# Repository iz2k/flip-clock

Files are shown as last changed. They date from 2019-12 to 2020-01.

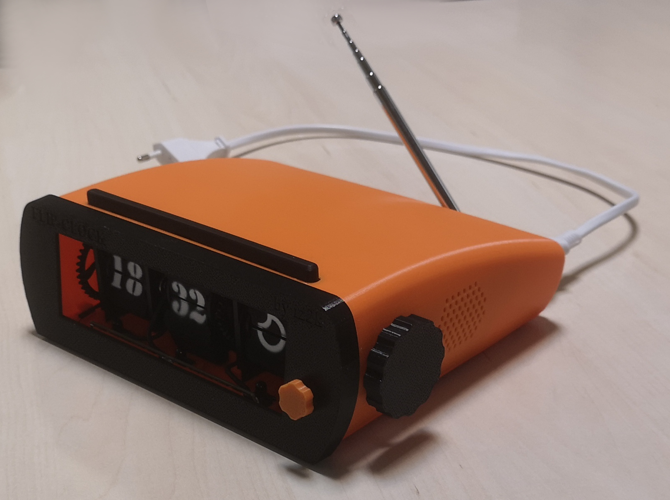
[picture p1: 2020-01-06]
imgs/right.jpg

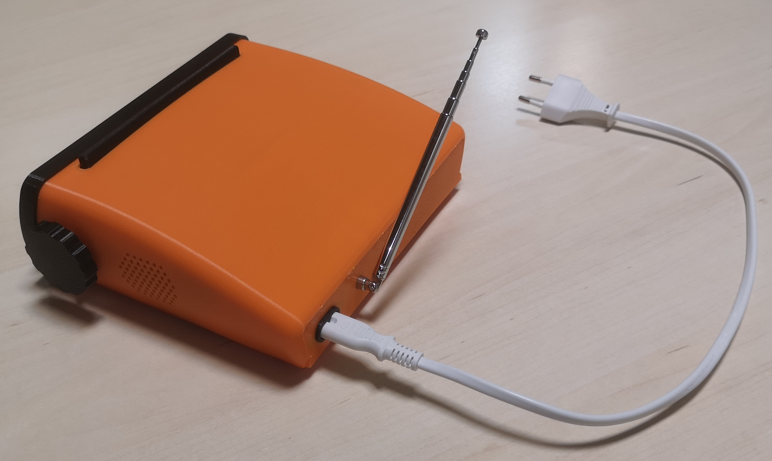
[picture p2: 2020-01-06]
imgs/back.jpg

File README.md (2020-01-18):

# Flip-Clock

The Flip-Clock is an old stylish, classic alarm clock with up to date features, such as automatic time adjustment, weather forecast, FM radio or Spotify playback. The device consists of three 3D printed flip digits, a  PCB with integrated drivers for the digit controlling stepper motors and a Raspberry Pi 3 A+ with 3W speakers to run the main code.

All the mechanics and electronics are mounted within an 3D printed elegant cover. Additionally, a snoozer bar, two rotary encoders and a RGBW LED strip are included for the user interface.

| front | right |
| - | - |
| left | back |

Find additional info about each design in:
* <a href="https://github.com/iz2k/flip-clock/tree/master/3d">3D parts</a>
* <a href="https://github.com/iz2k/flip-clock/tree/master/pcb_hw">PCB hardware</a>
* <a href="https://github.com/iz2k/flip-clock/tree/master/pcb_fw">PCB firmware</a>
* <a href="https://github.com/iz2k/flip-clock/tree/master/rpi_sw">RPi3 software</a>

Flip-Clock in action (https://youtu.be/fy7IPMUoMU4 "Flip-Clock in action")

# Parts

## 3D printed flip digits

Each flip digit consists of a support structure with two bearings. The axle is placed inside the bearings holding two flap holders. All the flaps are mounted within those holders. The movement of the digit is achieved with a stepper motor and two gears. An IR transmitter and an IR receiver are palced on the top and on the bottom of the flaps to detect transitions. Additionally, a limit switch is placed close to the gears to synchronize with it each turn.

### Subparts

1. Support structure
2. Bearings (<a href="https://www.amazon.es/gp/product/B07CWLGNJ5/ref=ppx_yo_dt_b_asin_title_o07_s01?ie=UTF8&psc=1">623-2RS</a>)
3. Axle
4. Flap holders
5. Flaps
6. Gears
7. Stepper motor (<a href="https://www.amazon.es/gp/product/B07LCFKJB8/ref=ppx_yo_dt_b_asin_title_o01_s00?ie=UTF8&psc=1">28BYJ-48</a>)
8. IR transmitter (<a href="https://www.amazon.es/gp/product/B07F3W2SP4/ref=ppx_yo_dt_b_asin_title_o07_s00?ie=UTF8&psc=1">IR diode</a>)
9. IR receiver (<a href="https://www.amazon.es/gp/product/B07F3W2SP4/ref=ppx_yo_dt_b_asin_title_o07_s00?ie=UTF8&psc=1">IR photodiode</a>)
10. Limit switch (<a href="https://www.amazon.es/gp/product/B07GKS9XC7/ref=ppx_yo_dt_b_asin_title_o05_s00?ie=UTF8&psc=1">CLW1093</a>)



## FlipDigitController PCB
The FlipDigitController PCB includes a microcontroller and drivers to control the stepper motors. Additionally, the PCB also handles the IR transmitter and receiver to detect flap transitions and the limit switch for automatic synchronization of the axle. The PCB has an UART interface for the abstraction layer protocol.

The current version of the PCB can handle up to two flip digits at the same time. For the FlipClock device two units of the PCB have been used: one to control hours and minutes flaps, and another one to control weather flaps.

| Block diagram | Layout |
|---|---|
| | |

### Subparts
1. <a href="http://www.ti.com/product/MSP430FR2433">MSP430FR2433 MCU</a>
2. <a href="http://www.ti.com/product/INA333?keyMatch=INA333&tisearch=Search-EN-everything&usecase=part-number">INA333 comparators</a>
3. <a href="https://www.ti.com/product/ULN2003A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">ULN2003A drivers</a>

## 3D printed cover


### Subparts
1. 3D printed top cover
2. 3D printed bottom cover
3. 3D printed front cover
4. 3D printed back cover

## Rotary encoders
For the user interface two rotary encoders have been used. The used encoders can detect steps in both directions, and include a built-in switch. One of the encoders is used to control the volume (up/down/mute), whereas the other encoder controls the audio device (FM Radio/Spotify/OFF)

| Wheels | Encoders |
| --- | --- |
|| |

### Subparts
1. 3D printed volume wheel
2. 3D printed control wheel
3. <a href="https://www.mouser.es/ProductDetail/BI-Technologies-TT-Electronics/EN11-HSM1AF15?qs=u1MaZ2%2F4xgsleMatSs8Sqg==">TT EN11-HSM1AF15</a> Rotary Encoders

## Snooze bar
A snooze bar is included on top of the FlipClock device. This bar can be used to trigger the nightlight by default, or to stop/snooze the alarm when it has been triggered. Tactile switches are placed under the bar to detect when it is pressed.

| Bar | Switch |
| --- | --- |
|bar | switch

### Subparts
1. 3D printed snooze bar
2. <a hlink="https://octopart.com/evq-q2s03w-panasonic-1199659">EVQ-Q2S03W</a> tactile switches

## NeoPixel RGBW Stick
Two NeoPixel RGBW LED sticks have been included in the front of the FlipClock in order to provide nightlight and light-sign functions to the device.

neopixel

### Subparts
1. <a href="https://www.adafruit.com/product/2868">NeoPixel RGBW Stick</a>

## 3W Speakers


### Subparts
1. <a href="https://www.adafruit.com/product/1669">Stereo Enclosed Speaker Set - 3W 4 Ohm</a>

## FM radio tunner (RTL-SDR)

| RTL-SDR dongle | FM antenna |
| --- | --- |
|||

### Subparts
1. <a href="https://www.amazon.es/gp/product/B013Q94CT6/ref=ppx_yo_dt_b_asin_title_o06_s00?ie=UTF8&psc=1">RTL-SDR dongle</a>
2. <a href="https://www.amazon.es/gp/product/B07CJYRWXQ/ref=ppx_yo_dt_b_asin_title_o01_s00?ie=UTF8&psc=1">FM antenna</a>

## Raspberry Pi 3 A+
|Raspberry Pi 3 Model A+|Adafruit I2S 3W Stereo Speaker Bonnet|
|--|--|
|||

### Subparts
1. <a href="https://www.raspberrypi.org/products/raspberry-pi-3-model-a-plus/">RPI3 A+</a>
2. <a href="https://www.adafruit.com/product/3346">Adafruit I2S 3W Stereo Speaker Bonnet</a>

## Power Supply
|Power Supply Module| PSM Housing|
|--|--|
|||

### Subparts
1. <a href="https://www.digikey.com/product-detail/en/mean-well-usa-inc/PS-05-5/1866-5411-ND/7705819">PS-05-5</a> power supply module
2. 3D printed housing

# Wiring

The correct wiring to connect the different electronics is as follows:

PSM connection:

| Subpart | PIN | PIN | Subpart |
| -- | -- | -- | --|
| RPI3 | 5V | 5V | PSM |
| RPI3 | GND | GND | PSM |

NeoPixel connection:

| Subpart | PIN | PIN | Subpart |
| -- | -- | -- | --|
| NeoPixel | DIN | MOSI | RPI3 |
| NeoPixel | 5VDC | 5V | RPI3 |
| NeoPixel | GND | GND | RPI3 |

Snooze Bar connection:

| Subpart | PIN | PIN | Subpart |
| -- | -- | -- | --|
| Snooze Bar | SW0 | GPIO 4 | RPI3 |
| Snooze Bar | SW1 | GPIO 17 | RPI3 |

Volume Encoder<sup>1</sup> connection:

| Subpart | PIN | PIN | Subpart |
| -- | -- | -- | --|
| Volume Encoder | SW0 | GPIO 24 | RPI3 |
| Volume Encoder | SW1 | GPIO 25 | RPI3 |
| Volume Encoder | ROT0 | GPIO 27 | RPI3 |
| Volume Encoder | ROT1 | GPIO 23 | RPI3 |
| Volume Encoder | GND | GPIO 22 | RPI3 |

Control Encoder<sup>1</sup> connection:

| Subpart | PIN | PIN | Subpart |
| -- | -- | -- | --|
| Control Encoder | SW0 | GPIO 5 | RPI3 |
| Control Encoder | SW1 | GPIO 6 | RPI3 |
| Control Encoder | ROT0 | GPIO 12 | RPI3 |
| Control Encoder | ROT1 | GPIO 16 | RPI3 |
| Control Encoder | GND | GPIO 13 | RPI3 |

Flip-Clock-Controller PCB:

|Subpart | PIN | PIN | Subpart |
|--|--|--|--|
|RPI3 | 3.3V | 3.3V | Flip-Clock-Controller PCB 1 (HHMM)|
|RPI3 | 3.3V | 3.3V | Flip-Clock-Controller PCB 2 (WW)|
|RPI3 | TX | RX | Flip-Clock-Controller PCB 1 (HHMM)|
|Flip-Clock-Controller PCB 1 (HHMM) | TX | RX | Flip-Clock-Controller PCB 2 (WW)|
|Flip-Clock-Controller PCB 2 (WW) | TX | RX | RPI3|

1: For ease of connectivity, all pins of rotary encoders are routed to GPIOs. These GPIOs will be configured as required with pull resistors or fixed voltages via software.

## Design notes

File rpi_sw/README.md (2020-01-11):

# Flip-Clock RPI3 A+: software design

The software in the Raspberry Pi 3 Model A+ is in charge of controlling the global funtionality of the device. It connects to the internet to get the current time, weather forecast and audio streams. All of it is performed according to the user interaction with the rotatory wheels, snooze bar and configuration files.

The software is written in Python 3 and makes use of several python libraries and external CLI applications.

## RPI3 setup

In order to run the Flip-Clock software on the Raspberry Pi 3 Model A+, the device has to be set up correctly. The software has been developed and tested on the `Raspbian Buster Lite (2019-09-26)` OS (without desktop). In any case, it should be possible to run it on other versions of Raspian.

### WPA supplicant

The first parameter to set up is the WiFi connectivity. The Model A+ does not have an ethernet connector, so the connectivity to internet is provded by WiFi. The easiest way to get the wifi connection working, is to use the WPA supplicant. As explained in <a href="https://howchoo.com/g/ndy1zte2yjn/how-to-set-up-wifi-on-your-raspberry-pi-without-ethernet">this</a> post, you need to include a file called `wpa_supplicant.conf` in the `/etc/wpa_supplicant/` folder.

This can also be achieved connecting the SD card with Raspian to your Windows/MacOS computer and copying the `wpa_supplicant.conf` file into the FAT32 `/boot` partition. Raspian will copy the file to the correct location in the next boot of the pi.

The content of the file has to be as follows:

````
ctrl_interface=DIR=/var/run/wpa_supplicant GROUP=netdev
update_config=1
country=ES

network={
	ssid="My SSID"
	psk="My Password"
	key_mgmt=WPA-PSK
}
````

You can add multiple networks if you want the device to connect to the internet in different locations.

### I2S audio (PWM)

In order to make the sound work with the Adafruit I2S 3W Stereo Speaker Bonnet, you can use the <a href="https://github.com/adafruit/Raspberry-Pi-Installer-Scripts">script on their github</a>. If you do not want to deep in in the details, just run the following curl script:

If you do not have curl already installed on your system, just do it:

````
sudo apt-get update
sudo apt-get install curl
````

And then execute the script:

````
curl -sS https://raw.githubusercontent.com/adafruit/Raspberry-Pi-Installer-Scripts/master/i2samp.sh | bash
````

### UART

The UART is required to communicate with the Flip-Clock-Contorller PCB. As by default in Raspian the UART is assigned to the console, you will need to disable the console and enable the software UART `/dev/ttyS0`.

This can be easily achieved using the `raspi-config` tool. Go to the `Interfacing Options` section, and then to `Serial`.

### SPI

In order to control the NeoPixel stick, we will use the <a href="https://github.com/jgarff/rpi_ws281x">rpi_ws281x</a> python library. This library supports controlling the stick using PCM, PWM or SPI. Given that we are using PCM for audio and PWM for PiGPIO (see in dependencies), we will use the SPI for the NeoPixel stick.

Many distributions have a maximum SPI transfer of 4096 bytes. This can be changed in /boot/cmdline.txt by appending

````
spidev.bufsiz=32768
````

On the RPi 3 you have to change the GPU core frequency to 250 MHz, otherwise the SPI clock has the wrong frequency. Do this by adding the following line to /boot/config.txt and reboot.

````
core_freq=250
````

SPI requires you to be in the gpio group if you wish to control your LEDs without root.

## Dependencies

Once the hardware of the Raspberry Pi has been correctly set-up, the dependencies of the project have to be installed.

### Python 3

Given that the Flip-Clock software is written in python, you will need the correct interpreter. Install python 3 as follows:

````
sudo apt-get install python3
````

Additionally, you will need to install several dependencies referenced in the project using `pip3`:

````
sudo pip3 install time
sudo pip3 install os
sudo pip3 install datetime
sudo pip3 install rpi_ws281x
sudo pip3 install pigpio
sudo pip3 install queue
sudo pip3 install wave
sudo pip3 install alsaaudio
sudo pip3 install subprocess
sudo pip3 install shlex
sudo pip3 install darksky
sudo pip3 install lxml 
sudo pip3 install subprocess
sudo pip3 install shlex
sudo pip3 install flask
sudo pip3 install threading
sudo pip3 install wtforms 
sudo pip3 install decimal
````

I may be missing some module. In case you get an error of some module missing, just install it using `pip3`.

### PiGPIO (PWM)

<a href="http://abyz.me.uk/rpi/pigpio/index.html">PiGPIO</a> is a library for the Raspberry Pi which allows control of the General Purpose Input Outputs (GPIO). This library has been selected as it provides a fast response time, which is required for the rotary encoders.

Install the PiGPIO deamon as follows:

````
sudo apt-get update
sudo apt-get install pigpio python-pigpio python3-pigpio
````

In order to make the pigpio deamon run on startup you can either enable it via systemctl, or add a root crontab job. 

As explained in <a href="https://www.raspberrypi.org/forums/viewtopic.php?t=103752#p717150">this</a> post, use

````
sudo crontab -e
````

to edit the root crontab and add the following line to the end. Then ctrl-o return ctrl-x to exit.

````
@reboot              /usr/bin/pigpiod -t 0
````

Note that it is necessary to use the `-t 0` argument in order to launch the `pigpio` deamon in `PWM` mode instead of the default `PCM` mode. Failing to do so will break the audio that is already using the PCM hardware.

### mplayer

In order to play audio files, or in this case to play the audio returned by google translate for TTS purposes, install `mplayer`:

````
sudo apt-get install mplayer
````

### SoftFM

In order to synthonize FM radio using the RTL-SDR stick, we will use an improved version of `rtl_fm` called `softfm`. It gets better results with poor quality radio signals. We will have to build the binary for the RPI3 ourselves, but it is quite straightforward.

#### Install RTL-SDR

First install the RTL-SDR library in order to have the required header files.

````
sudo apt-get install rtl-sdr
````

You can check if the RTL-SDR usb dongle is recognized as follows:

````
rtl_test
````

Yous should see something similar to this:

````
Found 1 device(s):
  0:  Generic, RTL2832U, SN: 77771111153705700
````

#### Build SoftFM

As explained in the <a href="https://github.com/jorisvr/SoftFM">SoftFM github repository</a>, to install SoftFM, download and unpack the source code and go to the top level directory. 

First make sure you have the build tools installed:

````
sudo apt-get install libusb-1.0-0-dev
sudo apt-get install build-essential
````

Then do like this:

````
mkdir build
cd build
cmake ..

make
````

You can test if the generated binary works fine:

````
./softfm -f <radio-frequency-in-Hz>
````

### Tizonia
<a href="http://tizonia.org/">Tizonia</a> is a cloud music player from the Linux terminal. It supports some of the major cloud music services: Spotify, Google Play Music, SoundCloud, YouTube, Plex and Chromecast. We will use this CLI player to add playback support from Spotify. It should be straightforward to extend playback support for the other supported audio streaming platforms, but this has not been implemented for now, as I am currently a Spotify user.

Install Tizonia as follows:

````
curl -kL https://github.com/tizonia/tizonia-openmax-il/raw/master/tools/install.sh | bash
````

### Raspotify (optional)

Even if Tizonia is great and allows us to stream music from spotify from code, it will not show our Flip-Clock as a Spotify device in our network. If you want to use the Flip-Clock as a smart speaker that shows as a spotify device and can be controlled by your smartphone, just install Raspotify. This is optinal, as the rest of the software does not depend on raspotify to function.

To install raspotify, follow the instructions on the <a href="https://github.com/dtcooper/raspotify">Raspotify github repository</a>:

````
curl -sL https://dtcooper.github.io/raspotify/install.sh | sh
````

## Flip-Clock software

In order to run the Flip-Clock software, just copy all the files to the desired location. I used `/usr/share/flip-clock`. for ease of use, make the main file executable:

````
chmod +x flip-clock.py
````

You can also add a symbolic link to `/usr/bin` in order to make it visible to $PATH.

````
ln -s /usr/share/flip-clock/flip-clock /usr/bin/flip-clock
````

To run the software, just execute it:

````
./flip-clock
````

### Autostart (systemd unit file)

In order to make the Flip-Clock software run automatically on every boot, you can create a systemd unit file. I have included a reference unit file in the `autostart` folder.

Copy the flip-clock.service file to `/etc/systemd/system/` folder:

````
sudo cp  flip-clock.service /etc/systemd/system/ flip-clock.service
````

The reference unit file redirects the output to syslog using the method explained <a href="https://stackoverflow.com/questions/37585758/how-to-redirect-output-of-systemd-service-to-a-file">here</a>. In order to configure syslog to handle the incoming stream, copy the `flip-clock.conf` configuration file to `/etc/rsyslog.d/`

````
sudo cp flip-clock.conf /etc/rsyslog.d/
````

Now make the log file writable by syslog:

````
chown root:adm /var/log/flip-clock.log
````

Restart rsyslog:

````
sudo systemctl restart rsyslog
````

Now the stdout/stderr of flip-clock will still be available through journalctl (`sudo journalctl -u flip-clock`) but they will also be available in `/var/log/flip-clock.log`.

Reload the systemctl daemon to read the new unit file.

````
sudo systemctl daemon-reload
````

Enable the flip-clock service to run on startup:

````
sudo systemctl enable flip-clock.service
````

Run the flip-clock service without rebooting:

````
sudo systemctl start flip-clock.service
````

### Code structure

The code structure is as follows:

````
flip-clock
 >> /config/
    >> Configuration XML files.
 >> /frontend/
    >> Flask web frontend files.
 >> /lib/
    >> Project specific library files.
 >> /sounds/ 
    >> PCM format sound files.
 >> flip-clock.py
    >> Main program.
````

#### Main program

The main program generates instances of the library classes to control the different peripherals, and keeps track of the main program flow with the user interaction. The callbacks of the rotary encoders and switches as well as the frontend event queue are read in this script to obtain the desired functionality.

#### Libraries

For each peripheral a project specific library has been created.

##### Clock

The clock library gets the current time from the system, the weather forecast form the DarkSky API and handles the UART communication towards the FlipClockPCB accordingly.

##### Audio

The audio library controls the audio of the device through alsamixer. It controls the volume and allows playing simple PCM files and converting text to audio using google translate as TTS.

##### LED

The LED library controls the Neopixel sticks to generate light signaling as requested by the main program.

##### IO

The IO library handles the rotary encoders and switches.

##### Spotify

The Spotify library handles the spotify playback through Tizonia.

##### Radio

The Radio library handles the radio synthonization through SoftFM.

##### Alarm

The Alarm library handles the alarm settings to trigger the corresponding events when the time comes.

#### Front-end (flask)

The flask based web front-end allows the user to configure the clock, radio stations, spotify playlists and alarm configurations via a web browser accesible through: `http://hostname:5000`

#### Configuration files

The configuration files store the configuration of the different services.

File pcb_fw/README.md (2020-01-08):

# Flip-Clock-Controller PCB: firmware design

The firmware of the Flip-Clock-Controller PCB has been designed using Code Composer Studio. The device is controled via standard UART communication at 115200 bauds. Here are the supported commands. The commands are decoded after receiving a return character.

| Command | Description |
|--|--|
| i | Shows current situation of HH and MM digits |
| hXX | Move HH digit to poxition XX (where XX are two decimal digits) |
| mXX | Move MM digit to poxition XX (where XX are two decimal digits) |
| sh | Sync HH digit. Keeps on moving flaps until the limit switch finds the synchronization position. |
| sm | Sync MM digit. Keeps on moving flaps until the limit switch finds the synchronization position. |
| chXX | Calibrate HH value in synchronization position to XX (where XX are two decimal digits)|
| cmXX | Calibrate MM value in synchronization position to XX (where XX are two decimal digits)|

In order to add the weather forecast digit, a second Flip-Clock-Controller PCB has been used. For control simplicity, and given that the PCB echoes the received UART characters, the UART of the two PCBs have been connected in daisy-chain.

|Subpart | PIN | PIN | Subpart |
|--|--|--|--|
|RPI3 | TX | RX | Flip-Clock-Controller PCB 1 (HHMM)|
|Flip-Clock-Controller PCB 1 (HHMM) | TX | RX | Flip-Clock-Controller PCB 2 (WW)|
|Flip-Clock-Controller PCB 2 (WW) | TX | RX | RPI3|

For the second PCB, a modified version of the firmware has been used, where the following commands are included:

| Command | Description |
|--|--|
| y | Shows current situation of WW digit |
| wXX | Move WW digit to poxition XX (where XX are two decimal digits) |
| sw | Sync WW digit. Keeps on moving flaps until the limit switch finds the synchronization position. |
| cwXX | Calibrate WW value in synchronization position to XX (where XX are two decimal digits)|

## Flashing the MSP430

I have used a <a href="http://www.ti.com/tool/MSP-FET">MSP-FET</a> device as I already own one. If you do not have one, a basic <a href="http://www.ti.com/tool/MSP-EXP430FR2433?keyMatch=MSP430FR2433%20LAUNCHPAD&tisearch=Search-EN-everything">launchpad</a> can be used to program an external device. Finally, it is also possible to flash the device via the UART BSL using <a href="http://www.ti.com/tool/UNIFLASH?keyMatch=UNIFLASH&tisearch=Search-EN-everything&usecase=part-number">Uniflash</a> software.

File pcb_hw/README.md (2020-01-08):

# Flip-Clock-Controller PCB: hardware design

The Flip-Clock-Controller PCB has been designed using Circuit Maker. Unluckily, there is now way to export the design to standard design formats out of their cloud. Thus, only the fabrication outputs and the documentation is included.

The Flip-Clock-Contorller PCB features a low power MSP430FR2433 microcontroller to handle the control of the flap digits. For each digit a stepper motor driver is included. The PCB also includes the analog front-end to handle the IR transmitter and receiver so that each time a flap falls down the MCU can detect it. Additionally, a limit switch is included so that every time the gear return to the initial position the MCU can detect the position and synchronize continuously to avoid number offset due to missed flap transitions (that rarely happen). The control interface of the PCB is 3.3V UART.

Even if a integrated 5V to 3.3V DCDC is included in the design, I finally decided to bypass it and use the 3.3V provided by the Raspberry Pi 3. The rest of the components are easy to solder manually with a soldering air gun.



## Schematics



## Layout



## 3D



## Fabrication outputs

The following fabrication outputs are included:
* Gerber files
* NC Drill files
* Bill Of Materials

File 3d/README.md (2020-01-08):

# Flip-Clock 3D design

The design of the 3D printed parts has been done using Fusion 360. The document flip-clock.f3d contains the complete design, including the external electronic components.

For the internal parts of the Flip Digits, ABS filament has been used for enhanced mechanical robustness. Same for the bottom part of the cover itself.

| Internal view | External view|
|--|--|
| | |

However, for the other parts of the cover, PLA filament has been used for ease of printing.

## Flip Digits

The most important part of the design are the flip digits. Those are composed by the support structure, axle with the gears, flap-holders and the flaps themselves. Additionally, the structure includes holders for th IR transmitter, IR receiver and the synchronization limit switch.

There are two different flap-holder sizes: one for 24 flaps, and another one for 60 flaps. The size of 24 is used for hours and weather flaps, whereas the size of 60 is for the minutes.



### Flaps

The flaps are quite tricky to print because of their thinness. I have found that using PLA filament and printing them in vertical position gets the best results. Note that the flaps for the 24 size flap-holders and the ones for the 60 size flap-holders are slightly different.



Once you get the flaps printed, it's time to add the content. In my case I have drawn the numbers and the weather icons using a white painting spray. In order to get good drawings, I have designed and printed the stencils, so that you have only to insert two flaps and spray them to get the desired drawing on them. The stencil parts are also included in the repositoyry, under the `/3d/etc/stencil` directory



## Cover

As mentioned earlier, I found it easier to print the cover with PLA filament, but feel free to try other options. In this case, the most complicated part is the top cover. In my case, y got nice prints placing the cover in vertical position. aDDing some supports also helps.



The different parts of the cover should be tied together using standard M2*6 screws.

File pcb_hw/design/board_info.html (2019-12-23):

Altium

# Board Information

Date: | | 23/12/2019
Time: | | 11:28:09
Elapsed Time: | | 00:00:00
Filename: | | LAYOUT.CMPcbDoc
Units: | | mmmils

General
Horizontal Dimension, max | 34.163mm
Vertical Dimension, max | 35.941mm
Total surface area
Copper layer count | 2
Smallest electrical gap/space | -
Smallest track width | 0.0254mm
Smallest hole size | 0.3mm
Biggest hole size | 2mm
Number of plated through holes | 63
Number of plated slots | 0
Number of unplated holes | 0
Number of unplated slots | 0
Number of cutouts | 1

Back to top

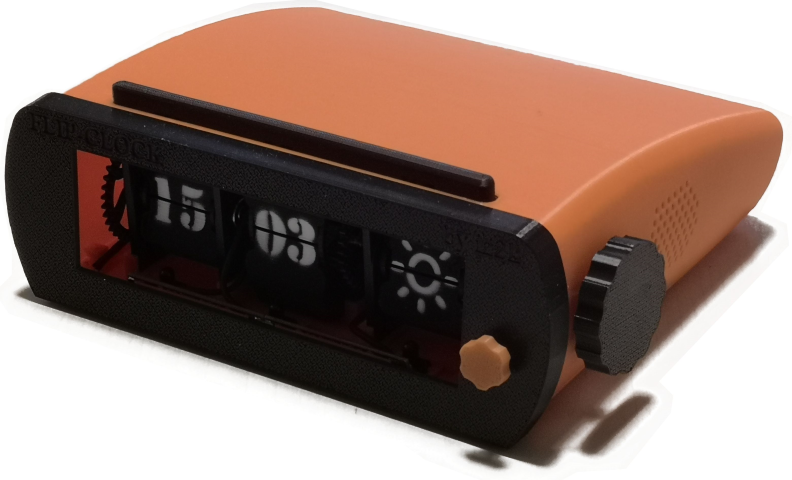
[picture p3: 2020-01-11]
rpi_sw/flip-clock/frontend/img/flipclock.png

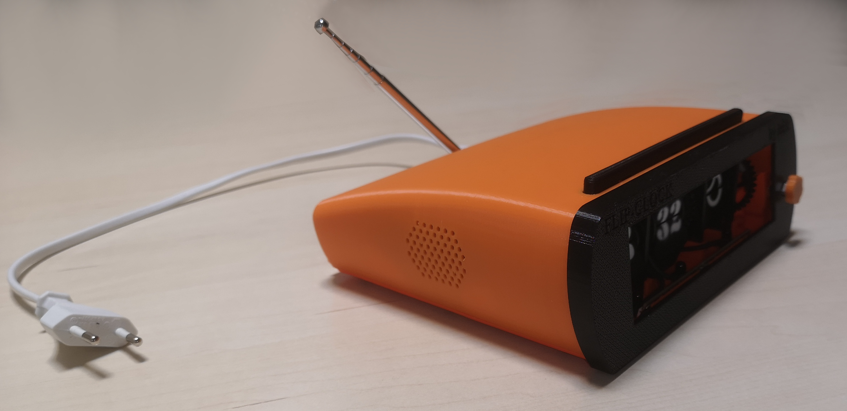
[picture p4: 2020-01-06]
imgs/left.jpg

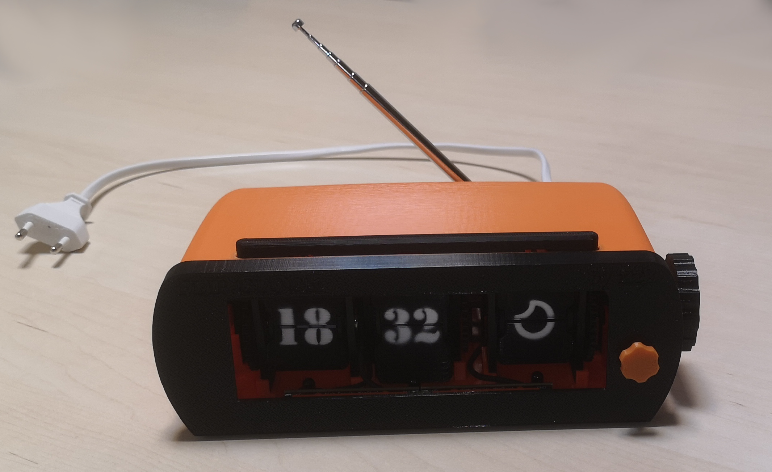
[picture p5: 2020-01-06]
imgs/front.jpg

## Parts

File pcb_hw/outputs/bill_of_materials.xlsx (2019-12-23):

Designator | Component | Description
C1, C2 | cap 22uF | SMD Multilayer Ceramic Capacitor, GRM Series, 22 uF, 20%, X5R, 6.3 V, 0603 [1608 Metric]
C3 | Vitramon VJ0603Y332KXAAC | Multilayer Ceramic Capacitors MLCC - SMD/SMT 3300pF 50volts X7R 0.1
CMP1, CMP2 | INA333AIDGKT | Low Power, Precision Instrumentation Amplifier, -40 to 125 degC, 8-pin SOP (DGK8), Green (RoHS & no Sb/Br)
DCDC | LMZ21701SILT | DC/DC CONVERTER, SYNCHRONOUS BUCK, 2.5MHZ, USIP; DC / DC Converter Type:Non Isolated POL; Input Voltage Min:3V; Input Voltage Max:17V; No. of Outputs:1; DC / DC Converter IC Case: SIP; No. of Pins:8;
DRV1, DRV2 | ULN2003APW | High-Voltage, High-Current Darlington Transistor Arrays 16-TSSOP -20 to 70
FW, LED | Samtec TSW-104-05-G-S | CONN HEADER 4POS .100" SGL GOLD
IRRX1, IRRX2, IRTX1, IRTX2, SYNC1, SYNC2 | Samtec TSW-102-05-G-S | CONN HEADER 2POS .100" SGL GOLD
MCU | Texas Instruments MSP430FR2433IRGET | 16 MHz Ultra-Low-Power Microcontroller with 16 KB FRAM, 4 KB RAM, 10-bit ADC, 19 IO, 4 16-bit Timers 24-VQFN -40 to 85
POW | CMP-668703-2 | 0.025" SQ Post Header, Through-hole, Vertical, -55 to 125 degC, 2.54 mm Pitch, 3-Pin, Male, RoHS
R01, R04, R05, R12, R22 | KOA Speer RK73B1JTTD103J | Res Thick Film 0603 10K Ohm 5% 1/10W ±200ppm/C Molded SMD Punched Paper T/R
R02 | Yageo RC0603FR-071M21L | Thick Film Resistors 1.21M OHM 1%
R03 | Yageo RT0603FRE07383KL | Thin Film Resistors 1/10W 383K ohm 1% 50ppm
R11, R13, R21, R23 | KOA Speer RK73H1JTTD1001F | Res Thick Film 0603 1K Ohm 1% 0.1W(1/10W) ±100ppm/C Molded SMD Automotive Punched Paper T/R
R14, R24 | KOA Speer RK73H1JTTD1000F | Res Thick Film 0603 100 Ohm 1% 0.1W(1/10W) ±100ppm/C Molded SMD Automotive Punched Paper T/R
STP1, STP2 | Samtec TSW-105-05-G-S | CONN HEADER 5POS .100" SGL GOLD
UART | TSW-103-07-F-S | 0.025" SQ Post Header, Through-hole, Vertical, -55 to 125 degC, 2.54 mm Pitch, 3-Pin, Male, RoHS

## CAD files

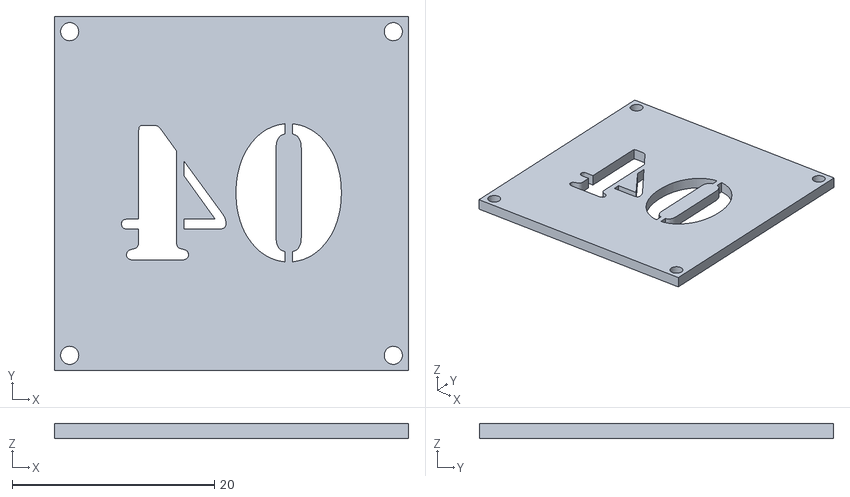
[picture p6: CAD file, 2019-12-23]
3d/etc/stencil/numbers/04.stl
35.0 x 35.0 x 1.50

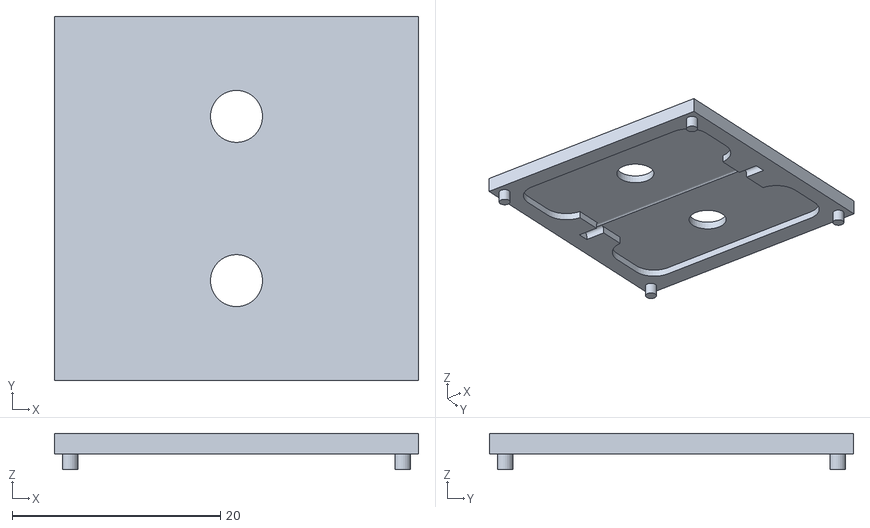
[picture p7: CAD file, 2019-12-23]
3d/etc/stencil/stencil base flap_24.stl
35.0 x 35.0 x 3.50

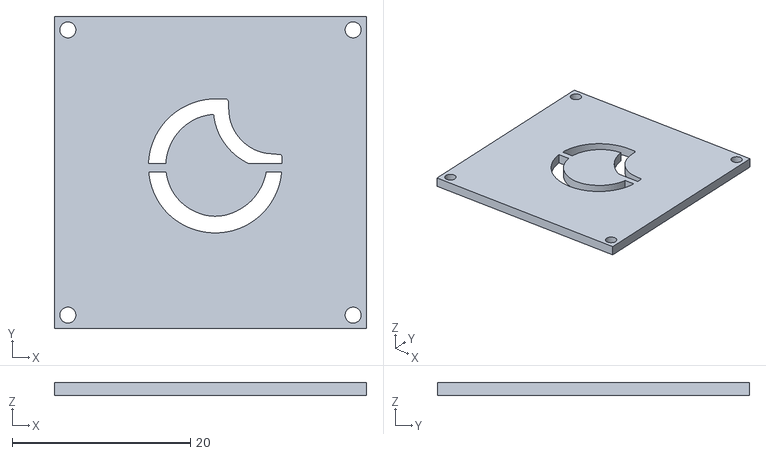
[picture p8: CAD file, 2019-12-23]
3d/etc/stencil/weather/02-clear-night.stl
35.0 x 35.0 x 1.50

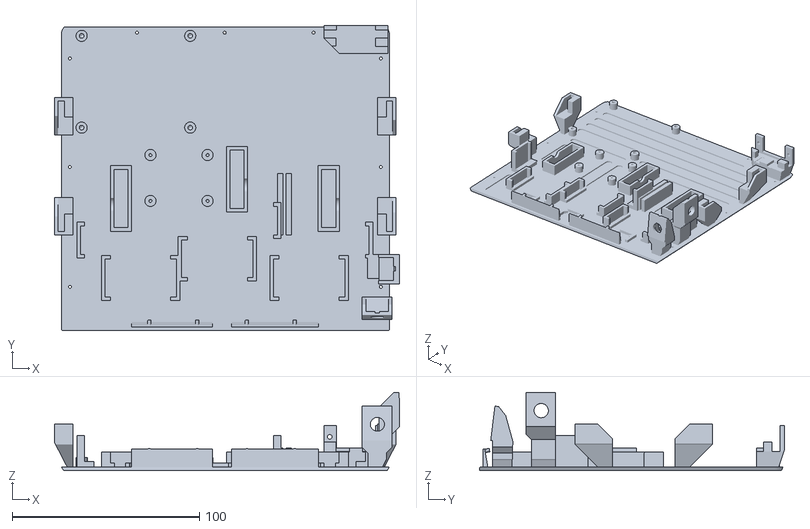
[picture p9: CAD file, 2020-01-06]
3d/parts/cover_bottom.stl
184.3 x 163.0 x 41.8

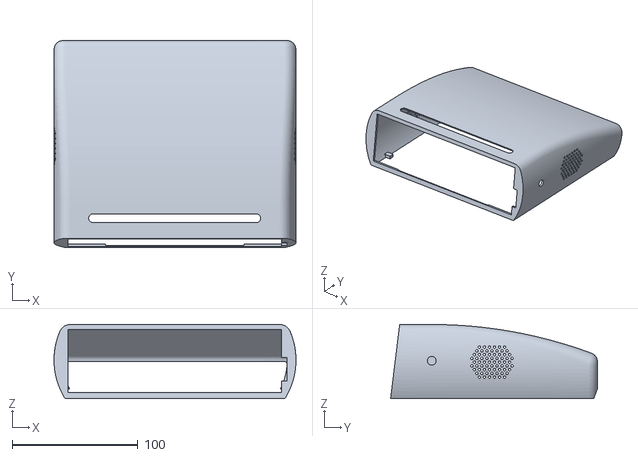
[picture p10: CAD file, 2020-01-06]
3d/parts/cover_top.stl
192.8 x 164.8 x 59.0

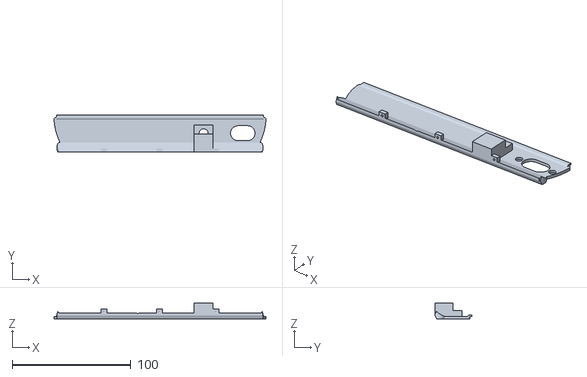
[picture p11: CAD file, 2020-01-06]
3d/parts/cover_back.stl
178.6 x 31.5 x 13.1

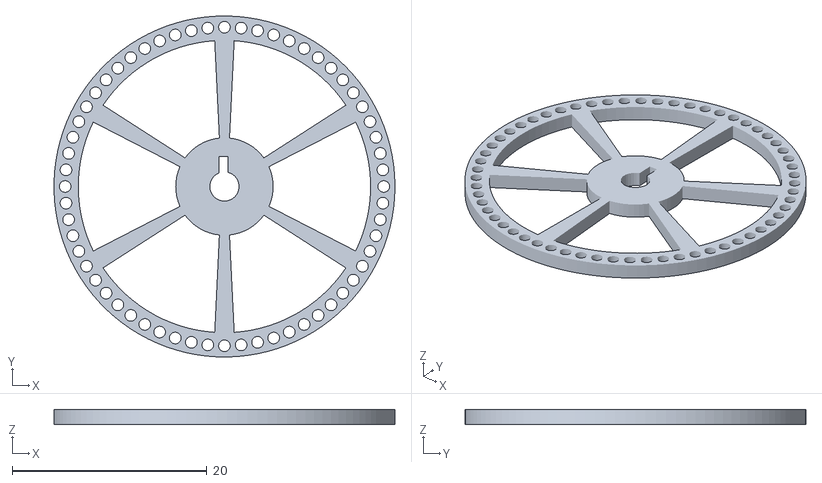
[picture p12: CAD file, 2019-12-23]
3d/parts/flapholder_60.stl
35.0 x 35.0 x 1.50

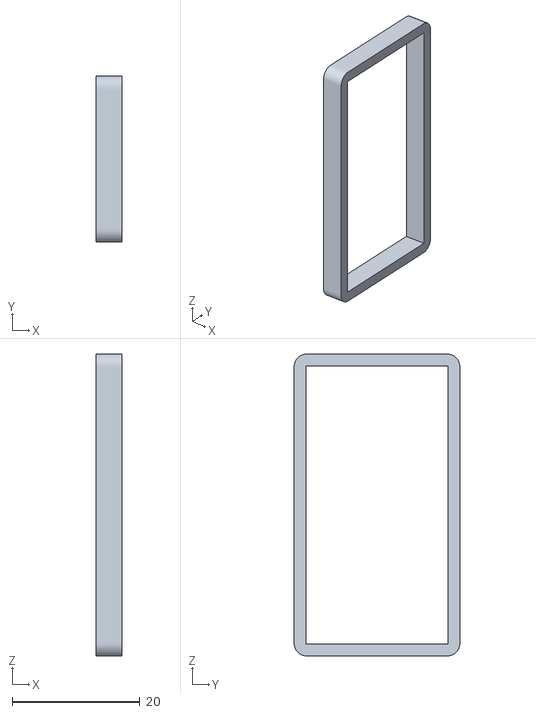
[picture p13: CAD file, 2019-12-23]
3d/parts/PSM_case_ring.stl
4.00 x 26.0 x 47.4

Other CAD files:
3d/etc/stencil/numbers/09.stl
3d/etc/stencil/stencil base flap_60.stl
3d/etc/stencil/weather/05-cloudy.stl
3d/etc/stencil/numbers/47.stl
3d/etc/stencil/weather/10-snow.stl
3d/etc/stencil/numbers/55.stl
3d/etc/stencil/weather/08-sleet.stl
3d/etc/stencil/numbers/25.stl
3d/etc/stencil/weather/04-partly-cloudy-night.stl
3d/etc/stencil/numbers/02.stl
3d/etc/stencil/numbers/00.stl
3d/etc/stencil/numbers/01.stl
3d/etc/stencil/numbers/03.stl
3d/etc/stencil/numbers/05.stl
3d/etc/stencil/numbers/06.stl
3d/etc/stencil/numbers/07.stl
3d/etc/stencil/numbers/08.stl
3d/etc/stencil/numbers/10.stl
3d/etc/stencil/numbers/11.stl
3d/etc/stencil/numbers/12.stl
3d/etc/stencil/numbers/13.stl
3d/etc/stencil/numbers/14.stl
3d/etc/stencil/numbers/15.stl
3d/etc/stencil/numbers/16.stl
3d/etc/stencil/numbers/17.stl
3d/etc/stencil/numbers/18.stl
3d/etc/stencil/numbers/19.stl
3d/etc/stencil/numbers/20.stl
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

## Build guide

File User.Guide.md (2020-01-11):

# Flip-Clock: User Guide

## Front buttons



The main functionality of the Flip-Clock is controlled with the front buttons. 

### Contorl wheel

The control wheel is a rotary encoder with integrated switch that is used to change the operation mode of the device. Each time you make a long push to the control wheel, the operation mode will switch.

Currently this is the operation mode sequence:
* Idle
* Spotify
* Radio

#### Spotify mode

While in spotify mode use the wheel as follows:

* Move clockwise: move the spotify player to the next song.
* Move counterclockwise: move the spotify player to the previous song.
* Short press: move the spotify player to the next playlist.
* Long press: Go to radio mode.

#### Radio mode

While in radio mode use the wheel as follows:

* Move clockwise: move the radio tuner to the next station.
* Move counterclockwise: move the radio tuner to the previous station.
* Short press: TBD.
* Long press: Switch off (go to idel mode).

### Volume wheel

The volume wheel allows changing the volume of the device as follows:

* Move clockwise: increment volume (2% steps).
* Move counterclockwise: decrement volume (2% steps).
* Short press: mute/unmute.
* Long press: TBD

### Snooze bar

The snooze bar can be used in two different scenarios: whilst an alarm is operational, or not.

#### No alarm operational

* Short press: turn on the nightlight (turns off automatically after 4 seconds)

#### Alarm is operational

* Short press: snooze the alarm. If enabled, the alarm will trigger again after the configured snooze time.
* Long press: turn off the alarm. The alarm will not longer trigger after the snooze time.

## Web front-end

In addition to the front buttons, the Flip-Clock has one more interface: an integrated web front-end. This web front-end can be accessed connecting to the port 5000 of the device:

````
http://flip-clock-pi:5000
````



### Clock

The clock fornt-end allows calibrating the Flip-Clock digits. This should be done once after manufacturing the clock. Note that whilst in calibration mode, the clock will not update with the current time.

| Clock (debug: off)  | Clock (debug: on) |
|--|--|
| |  |

#### Clock digits calibration

In order to calibrate a digit, follow this procedure:
* Click on `Sync XX`: this will triger the selected digit to start moving until the synchronization switch is reached. The digit will stop at the synchronization position.
* Set the current value in the digit box, and click on `Cal XX`
* Set a different value in the digit box, and click on `Set XX` to test if the digit has been properly calibrated.

For the weather digit calibration, keep in mind the following number to weather icon conversion table:

| Numer | Weather icon |
|--|--|
| 01 | Clear day |
| 02 | Clear night |
| 03 | Partly cloudy day |
| 04 | Partly cloudy night |
| 05 | Cloudy |
| 06 | Fog |
| 07 | Wind |
| 08 | Sleet |
| 09 | Rain |
| 10 | Snow |

Once all three digits have been calibrated, disable the debug mode to let the clock be updated with the current time and weather.

### Alarms

The alarm front-end allows configuring the desired alarms. You can configure as many alarms as you want.



The configuration parameters of the alarm are:

* Enable switch: enable/disable alarm.
* Alarm name: a name to recognize the alarm.
* Weekday switches: select to which weekdays the alarm applies.
* Alarm type: select if the alarm shall trigger the spotify player or the radio tuner.
* Alarm source: 
 * For spotify: the URI of the track or playlist to play.
 * For Radio: frequency to tune (in MHz).
* Shuffle switch: If the source is a playlist, enable/disable shuffling.
* Start volume: initial volume when the alarm triggers.
* End volume: final volume that the alarm will end up with after the specified ramp time.
* Ramp time: ram time (in minutes) for the volume ramp.
* Snooze switch: enable/disable snooze function.
* Snooze time: if enabled, time until the next alarm trigering after snooze bar has been pressed.
* Greeting switch: enable/disable greeting and weather forecast.
* Greeting text: custom text that the device will speak out loud prior to the weather forecast.
* Weather delay: delay (in minutes) from alarm trigger to weather forecast.

### Spotify

The spotify front-end allows configuring the spotify items (track/playlist) that will play in spotify mode.



The configuration parameters of the spotify items are:

* Name: a name to recognize the item.
* Shuffle switch : enable/disable shuffling.
* URI: Spotify URI (Uniform Resource Indicator) of the item.

The URI of a spotify item can be easily found in spotify right-clicking an item.

### Radio

The radio front-end allows configuring the radio stations that will be tuned in radio mode.



The configuration parameters of the radio stations are:

* Name: a name to recognize the item.
* Frequency : frequency (in MHZ) to be tuned.

The radio fornt-end also includes a real time radio control to tune the radio of the Flip-Clock at the desired frequency. This is useful to find the different radio stations during the configuration.

### Config

The configuration front-end allowd configuring credentials and other required values for the services such us spotify or DarkSky (for weather forecast).



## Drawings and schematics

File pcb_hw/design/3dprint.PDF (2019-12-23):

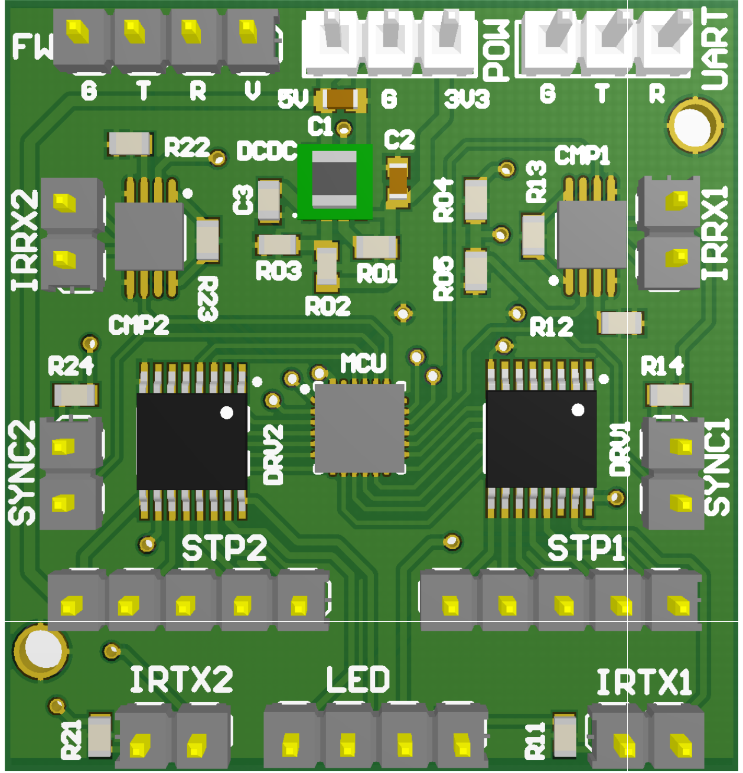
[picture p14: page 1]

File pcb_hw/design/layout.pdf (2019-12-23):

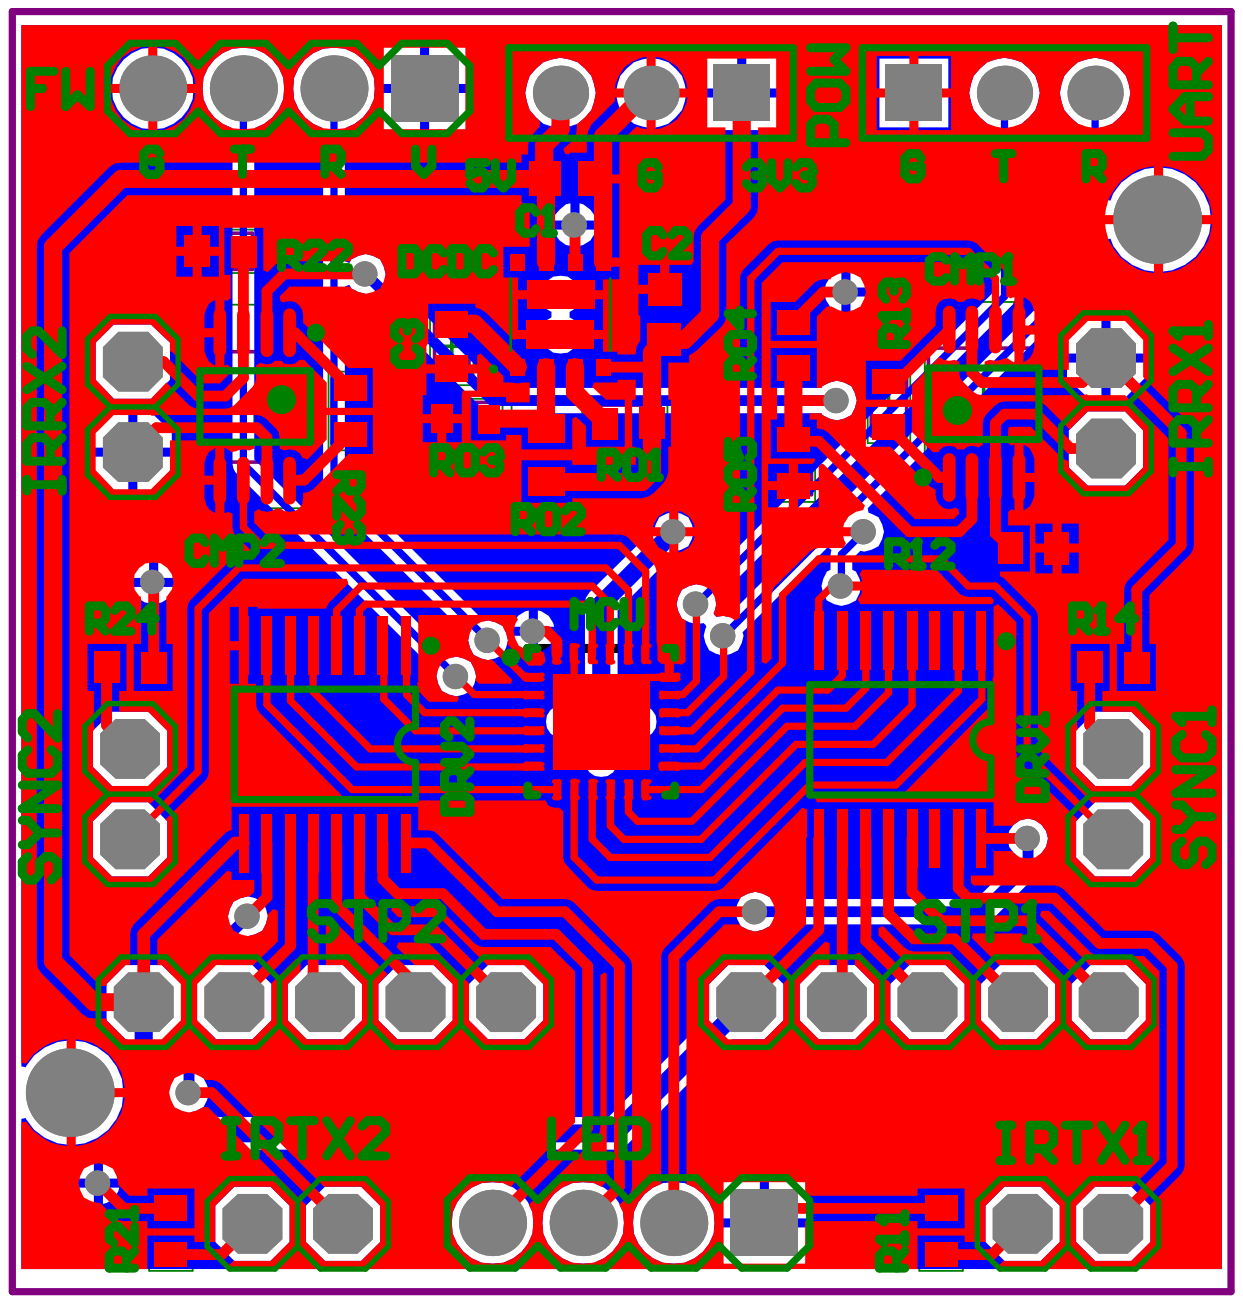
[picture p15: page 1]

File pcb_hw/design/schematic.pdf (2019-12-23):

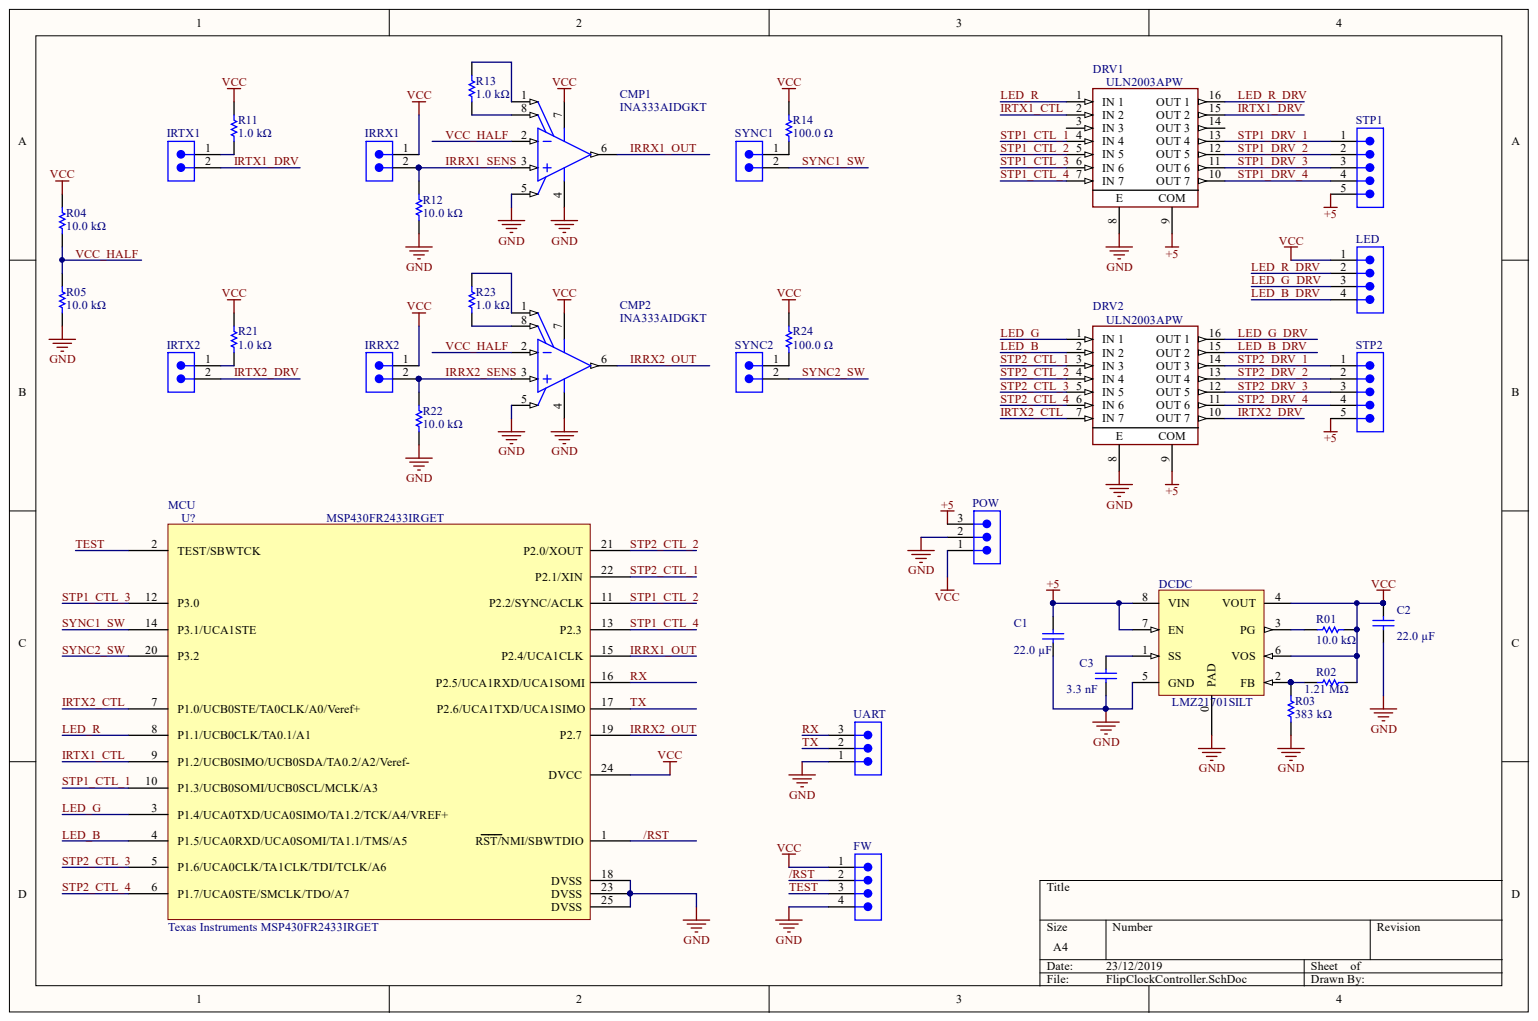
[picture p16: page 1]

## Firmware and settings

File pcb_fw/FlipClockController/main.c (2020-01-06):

#include <msp430.h> 
#include <stdint.h>
#include "hal/mcu.h"
#include "hal/ir-sensor.h"
#include "hal/sw-sensor.h"
#include "hal/stepper.h"
#include "hal/uart.h"

#define HH_DIVIDER  3
#define MM_DIVIDER  10

// Private routine prototypes
void decode_command();
void print_info();

// Shared variables
extern uint8_t fSystick;
extern uint8_t RxBuf[64];
extern uint8_t fCmd;
extern uint8_t fIRHH;
extern uint8_t fIRMM;

// Main varibales
uint8_t current_HH=1;
uint8_t current_MM=1;
uint8_t expected_HH=0;
uint8_t expected_MM=0;
uint8_t divcounter_HH=0;
uint8_t divcounter_MM=0;
uint8_t sync_HH_done=0;
uint8_t sync_MM_done=0;

#pragma PERSISTENT(cal_HH)
uint8_t cal_HH=0;
#pragma PERSISTENT(cal_MM)
uint8_t cal_MM=0;

uint8_t sync_delay_HH=0;
uint8_t sync_delay_MM=0;
#pragma PERSISTENT(cal_sdelay_HH)
uint8_t cal_sdelay_HH=00;
#pragma PERSISTENT(cal_sdelay_MM)
uint8_t cal_sdelay_MM=0;


typedef enum
{
    StatusStop,
    StatusRun,
    StatusFindSyncHH,
    StatusSyncDelayHH,
    StatusFindSyncMM,
    StatusSyncDelayMM,
} Status_t;

Status_t status=StatusRun;

/**
 * main.c
 */
void main(void)
{
    uint16_t nsteps_HH=0;
    uint16_t nsteps_MM=0;

	setup_mcu();
	setup_ir();
	setup_sw();
	setup_stepper();
	setup_uart();
	setup_systick();

    unlock_GPIOs();


    enable_IRTX1();
    enable_IRTX2();

    __bis_SR_register(GIE);

    while(1)
    {
        if (fSystick)
        {
            // Deassert flag
            fSystick=0;
            switch(status)
            {
            case StatusRun:
                // Check SYNC HH
                if(get_sync_HH())
                {
                    sync_delay_HH = 1;
                }
                if(sync_delay_HH !=0)
                {
                    if(sync_delay_HH++ > cal_sdelay_HH)
                    {
                        current_HH = cal_HH;
                        sync_HH_done = 1;
                        sync_delay_HH=0;
                    }
                }
                // Check SYNC MM
                if(get_sync_MM())
                {
                    sync_delay_MM = 1;
                }
                if(sync_delay_MM !=0)
                {
                    if(sync_delay_MM++ > cal_sdelay_MM)
                    {
                        current_MM = cal_MM;
                        sync_MM_done = 1;
                        sync_delay_MM=0;
                    }
                }
                // Check IRRX HH
                if (get_IR_HH())
                {
                    if (sync_HH_done) current_HH++;
                    if (current_HH>23) current_HH=0;
                    send_uart_string("H: ");
                    send_uart_int(current_HH);
                    send_uart_string(" (");
                    send_uart_int(nsteps_HH);
                    send_uart_string_nl(")");
                    nsteps_HH=0;
                }
                // Check IRRX MM
                if (get_IR_MM())
                {
                    if (sync_MM_done)current_MM++;
                    if (current_MM>59) current_MM=0;
                    send_uart_string("M: ");
                    send_uart_int(current_MM);
                    send_uart_string(" (");
                    send_uart_int(nsteps_MM);
                    send_uart_string_nl(")");
                    nsteps_MM=0;
                }
                // Control HH
                if (current_HH != expected_HH)
                {
                    if(divcounter_HH++>=HH_DIVIDER){
                        stepper_HH_move();
                        nsteps_HH++;
                        divcounter_HH=0;
                    }
                }else{
                    stepper_HH_stop();
                }
                // Control MM
                if (current_MM != expected_MM)
                {
                    if(divcounter_MM++>=MM_DIVIDER){
                        stepper_MM_move();
                        nsteps_MM++;
                        divcounter_MM=0;
                    }
                }else{
                    stepper_MM_stop();
                }
                break;
            case StatusFindSyncHH:

                // Check SYNC HH
                if(!get_sync_HH())
                {
                    if(divcounter_HH++>=HH_DIVIDER){
                        stepper_HH_move();
                        nsteps_HH++;
                        divcounter_HH=0;
                    }
                }else{
                    sync_delay_HH = 1;
                    status = StatusSyncDelayHH;
                }
                // Check IRRX HH
                if (get_IR_HH())
                {
                    send_uart_int_nl(nsteps_HH);
                    nsteps_HH=0;
                }
                break;
            case StatusFindSyncMM:
                // Check SYNC MM
                if(!get_sync_MM())
                {
                    if(divcounter_MM++>=MM_DIVIDER){
                        stepper_MM_move();
                        nsteps_MM++;
                        divcounter_MM=0;
                    }
                }else{
                    sync_delay_MM = 1;
                    status = StatusSyncDelayMM;
                }
                // Check IRRX HH
                if (get_IR_MM())
                {
                    send_uart_int_nl(nsteps_MM);
                    nsteps_MM=0;
                }
                break;
            case StatusSyncDelayHH:
                if(sync_delay_HH !=0)
                {
                    if(sync_delay_HH++ > cal_sdelay_HH)
                    {
                        stepper_HH_stop();
                        sync_delay_HH=0;
                        current_HH = cal_HH;
                        status = StatusStop;
                    }else{
                        stepper_HH_move();
                        nsteps_HH++;
                    }
                }
                // Check IRRX
                if (get_IR_HH())
                {
                    send_uart_int(nsteps_HH);
                    nsteps_HH=0;
                }
                break;
            case StatusSyncDelayMM:
                if(sync_delay_MM !=0)
                {
                    if(sync_delay_MM++ > cal_sdelay_MM)
                    {
                        stepper_MM_stop();
                        sync_delay_MM=0;
                        current_MM = cal_MM;
                        status = StatusStop;
                    }else{
                        stepper_MM_move();
                        nsteps_MM++;
                    }
                }
                // Check IRRX
                if (get_IR_MM())
                {
                    send_uart_int(nsteps_MM);
                    nsteps_MM=0;
                }
                break;
            }

        }

        if (fCmd)
        {
            // Deassert flag
            fCmd=0;
            // Decode command
            decode_command();
        }


    }
}

void decode_command()
{
    switch(RxBuf[0])
    {
    case 'h': // Set HOUR
    case 'H': // Set HOUR
        expected_HH = (RxBuf[1]-48)*10 + RxBuf[2]-48;
        break;
    case 'm': // Set MINUTES
    case 'M': // Set MINUTES
        expected_MM = (RxBuf[1]-48)*10 + RxBuf[2]-48;
        break;
    case 't': // Set Time HHMM
    case 'T': // Set Time HHMM
        expected_HH = (RxBuf[1]-48)*10 + RxBuf[2]-48;
        expected_MM = (RxBuf[3]-48)*10 + RxBuf[4]-48;
        break;
    case 's': // Find SYNC position
    case 'S': // Find SYNC position
        switch(RxBuf[1])
        {
        case 'h':
        case 'H':
            status = StatusFindSyncHH;
            break;
        case 'm':
        case 'M':
            status = StatusFindSyncMM;
            break;
        }
        break;
    case 'c': // CAL SYNC position values
    case 'C': // CAL SYNC position values
        switch(RxBuf[1])
        {
        case 'h':
        case 'H':
            SYSCFG0 = FRWPPW | DFWP;
            cal_HH = (RxBuf[2]-48)*10 + RxBuf[3]-48;
            SYSCFG0 = FRWPPW | PFWP | DFWP;
            current_HH = cal_HH;
            expected_HH = cal_HH;
            break;
        case 'm':
        case 'M':
            SYSCFG0 = FRWPPW | DFWP;
            cal_MM = (RxBuf[2]-48)*10 + RxBuf[3]-48;
            SYSCFG0 = FRWPPW | PFWP | DFWP;
            current_MM = cal_MM;
            expected_MM = cal_MM;
            break;
        }
        status = StatusRun;
        break;
    case 'd': // CAL SYNC DELAY value
    case 'D': // CAL SYNC DELAY value
        switch(RxBuf[1])
        {
        case 'h':
        case 'H':
            SYSCFG0 = FRWPPW | DFWP;
            cal_sdelay_HH = (RxBuf[2]-48)*10 + RxBuf[3]-48;
            SYSCFG0 = FRWPPW | PFWP | DFWP;
            break;
        case 'm':
        case 'M':
            SYSCFG0 = FRWPPW | DFWP;
            cal_sdelay_MM = (RxBuf[2]-48)*10 + RxBuf[3]-48;
            SYSCFG0 = FRWPPW | PFWP | DFWP;
            break;
        }
        status = StatusRun;
        break;
        case 'i': // SHOW INFO
        case 'I': // SHOW INFO
            print_info();
            break;
        case 'x': // STOP
        case 'X': // STOP
            status = StatusStop;
            break;
        case 'r': // STOP
        case 'R': // STOP
            status = StatusRun;
            break;
    }

}

void print_info()
{
    send_uart_string_nl("FlipClockController");
    send_uart_string_nl("-------------------");
    send_uart_string(" Current HH: ");
    send_uart_int_nl(current_HH);
    send_uart_string(" Current MM: ");
    send_uart_int_nl(current_MM);
    send_uart_string_nl(" Sync HH:");
    send_uart_string("  Cal: ");
    send_uart_int(cal_HH);
    send_uart_string("  Delay: ");
    send_uart_int_nl(cal_sdelay_HH);
    send_uart_string_nl(" Sync MM:");
    send_uart_string("  Cal: ");
    send_uart_int(cal_MM);
    send_uart_string("  Delay: ");
    send_uart_int_nl(cal_sdelay_MM);
}

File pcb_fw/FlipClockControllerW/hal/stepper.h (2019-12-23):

/*
 * stepper.h
 *
 *  Created on: 18 nov. 2019
 *      Author: IbonZalbide
 */

#ifndef HAL_STEPPER_H_
#define HAL_STEPPER_H_


// STEPPER HH CTL1:P2.1, CTL2:P2.0, CTL3:P1.6, CTL4:P1.7
#define STPHH_1_PDIR  P2DIR
#define STPHH_1_POUT  P2OUT
#define STPHH_1_BIT   BIT1
#define STPHH_2_PDIR  P2DIR
#define STPHH_2_POUT  P2OUT
#define STPHH_2_BIT   BIT0
#define STPHH_3_PDIR  P1DIR
#define STPHH_3_POUT  P1OUT
#define STPHH_3_BIT   BIT6
#define STPHH_4_PDIR  P1DIR
#define STPHH_4_POUT  P1OUT
#define STPHH_4_BIT   BIT7

// STEPPER MM CTL1:P1.3, CTL2:P2.2, CTL3:P3.0, CTL4:P2.3
#define STPMM_1_PDIR  P1DIR
#define STPMM_1_POUT  P1OUT
#define STPMM_1_BIT   BIT3
#define STPMM_2_PDIR  P2DIR
#define STPMM_2_POUT  P2OUT
#define STPMM_2_BIT   BIT2
#define STPMM_3_PDIR  P3DIR
#define STPMM_3_POUT  P3OUT
#define STPMM_3_BIT   BIT0
#define STPMM_4_PDIR  P2DIR
#define STPMM_4_POUT  P2OUT
#define STPMM_4_BIT   BIT3

void setup_stepper();
void stepper_HH_move();
void stepper_HH_stop();
void stepper_MM_move();
void stepper_MM_stop();

#endif /* HAL_STEPPER_H_ */

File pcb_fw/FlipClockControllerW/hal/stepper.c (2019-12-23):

/*
 * stepper.c
 *
 *  Created on: 18 nov. 2019
 *      Author: IbonZalbide
 */
#include <msp430.h>
#include <stdint.h>
#include "stepper.h"

const int8_t stepmtx [8][4] =
{
  {1, 0, 0, 0},
  {1, 1, 0, 0},
  {0, 1, 0, 0},
  {0, 1, 1, 0},
  {0, 0, 1, 0},
  {0, 0, 1, 1},
  {0, 0, 0, 1},
  {1, 0, 0, 1}
};

int8_t iStpHH=0;

void setup_stepper()
{
    // Set stepper control pins as output
    STPHH_1_PDIR |= STPHH_1_BIT;
    STPHH_2_PDIR |= STPHH_2_BIT;
    STPHH_3_PDIR |= STPHH_3_BIT;
    STPHH_4_PDIR |= STPHH_4_BIT;

    STPMM_1_PDIR |= STPMM_1_BIT;
    STPMM_2_PDIR |= STPMM_2_BIT;
    STPMM_3_PDIR |= STPMM_3_BIT;
    STPMM_4_PDIR |= STPMM_4_BIT;
}

void stepper_HH_move()
{
    stepmtx[iStpHH][0] ? (STPHH_1_POUT |= STPHH_1_BIT) : (STPHH_1_POUT &= ~ STPHH_1_BIT);
    stepmtx[iStpHH][1] ? (STPHH_2_POUT |= STPHH_2_BIT) : (STPHH_2_POUT &= ~ STPHH_2_BIT);
    stepmtx[iStpHH][2] ? (STPHH_3_POUT |= STPHH_3_BIT) : (STPHH_3_POUT &= ~ STPHH_3_BIT);
    stepmtx[iStpHH][3] ? (STPHH_4_POUT |= STPHH_4_BIT) : (STPHH_4_POUT &= ~ STPHH_4_BIT);
    if(++iStpHH>7)iStpHH=0;
}

void stepper_HH_stop()
{
    // Set signaling to 0
    STPHH_1_POUT &= ~ STPHH_1_BIT;
    STPHH_2_POUT &= ~ STPHH_2_BIT;
    STPHH_3_POUT &= ~ STPHH_3_BIT;
    STPHH_4_POUT &= ~ STPHH_4_BIT;
}

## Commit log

2019-12-22 [RPI_SW] > NIGHTLIGHT routine added to led library. > Snooze button invokes nightlight
2019-12-23 [3d] 3D design added: >> Fusion 360 design file >> Output STL files >> additional STL files for number and weather stencils
    [00.stl, 01-clear-day.stl, 01.stl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]
2019-12-23 [PCB_FW] FlipClockController firmware uploaded
    [main.c, stepper.c, stepper.h]
2019-12-23 [PCB_FW] FlipClockController firmware modified for single stepper, to be used with weather flaps
    [main.c, stepper.c, stepper.h]
2019-12-23 [PCB_HW] PCB design included. >> Design files: schematic and layout in pdf >> 3d model: STEP file >> Outputs: Gerber, NC Drills and BOM
    [LAYOUT.GBL, LAYOUT.GBO, LAYOUT.GBP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]
2019-12-23 [DOC] Wiring added
2019-12-31 flask frontend runs as separate thread from flip-clock main program
2019-12-31 Spotify and Radio navigation with rotary buttons improved
2020-01-02 Alarms initial trigger working. Simple Snooze working. Needs fix if snooze button is pressed after snooze time. Missing volume control. Missing greeting and weather forecast.
2020-01-06 FlipClockController PCB FW update. Clock stops with sync commands afetr sync reached. Necesary to send cal or run afterwards to continue operation.
    [main.c]
2020-01-06 Clock calibration through web frontend operational
2020-01-06 FM antenna replaced by external telescopic antenna.
    [FM_antenna_external.stl, FM_antenna_internal.stl, FM_antenna_top.stl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]
